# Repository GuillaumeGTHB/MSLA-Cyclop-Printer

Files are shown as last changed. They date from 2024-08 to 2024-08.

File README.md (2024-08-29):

# MSLA Cyclop Printer !
<p align="center">



</p>

If you like my work, you can help me by buying me a coffee, thank you! *https://buymeacoffee.com/guillaumehy or
 [paypal.me/guillaumehaouy](https://www.paypal.com/paypalme/guillaumehaouy)* <br />
*I should point out that I am a 20 year old student, it takes me a huge amount of time so don't be too harsh and impatient with me !* <br />
+ **A guide in .pdf format (English language, 64 pages for version 1.1) is included, it is a must-read, everything is explained in detail !** <br />
+ **NanoDLP is too huge for this repertory, you can download it at : https://www.nano3dtech.com/nanodlp-download/** <br />

**1. Introduction** <br />
**2. Technical details of the MSLA Cyclop printer** <br />
**3. Technical details of the Helios Curing station** <br />
**4. Pictures of my first prints (print tests take a lot of time, they are not yet 100% optimal)** <br />
**5. Schematics**
- A. Cyclop - 3D Printer
- B. Helios - Curing Station

## 1. Introduction
+ **Be careful! The resin severely attacks the printed plastic, as explained in the guide, you will need to apply a protective varnish on the tank as well as on the printing plate** <br />
+ Here you will find all the files and instructions on my homemade MSLA Cyclop v1.3 resin printer (and its Helios curing station) ! <br />
The CAD files (.step format) are available, the appropriate GRBl firmware as well as the NanoDLP version that I used. <br />
<p align="center">

 

 <br />
</p>

## 2. Technical details of the MSLA Cyclop printer <br />
+ Standalone printer (integrated slicer, just place an .stl file on a USB key) with Nextion 3.2" touch screen
+ Ultra-rigid structure in 2020 aluminum profiles
+ Ultra resolution axis ! Ball screw and two linear ball axes MGN12C
+ Electronics: Raspberry Pi 3B+ / Arduino Uno + Shield CNC v3 + A4988 driver (NanoDLP firmware for the RPI3B+, GRBL for the Arduino)<br />
+ Screen: 2k, 5.5" 1440p x 2560p <br />
+ Resolution: 47.25µm (0.04725mm) <br />
+ Printable area: 125x67x165mm <br />
+ UV power: 38W (adjustable in PWM with the M3 S1to1000 command) <br />
+ Approximate price: $450 <br />
+ Power supply: 12V 8A <br />
+ → more details in the .pdf guide <br />
<p align="center">




</p>

## 3. Technical details of the Helios Curing station <br />
+ Approximate power: 15W <br />
+ Turntable plate with adjustable timer <br />
+ Upward airflow (two 3010 fans: 30x10mm) <br />
+ Approximate price: $30 <br />
+ Minimum power supply: 12V 2A <br />
+ → more details in the .pdf guide <br />
<p align="center">




</p>

## 4. Pictures of my first prints
<p align="center">



</p>
<p align="center">


</p>

## 5. Schematics
### A. Cyclop
<p align="center">

</p>

### B. Helios
<p align="center">

</p>

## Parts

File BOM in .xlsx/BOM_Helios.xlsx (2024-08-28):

Name | Quantity | Links | Price | Total price
Timer module | 1 | https://fr.aliexpress.com/item/1005005994998871.html | 1.82 € | 1.82 €
LM2596 | 1 | https://fr.aliexpress.com/item/1082500515.html? | 0.94 € | 0.94 €
PWM 12V | 1 | https://fr.aliexpress.com/item/1005006462873434.html | 1.40 € | 1.40 €
16mm Led switch | 1 | https://fr.aliexpress.com/item/1005005617484886.html | 2.22 € | 2.22 €
3010 12V Fan | 2 | https://fr.aliexpress.com/item/1005003371996395.html | 0.99 € | 1.98 €
DC Jack Socket | 1 | https://fr.aliexpress.com/item/1005001368469076.html | 3.77 € | 3.77 €
Double side tape | /
Mirror tape | 5 | https://fr.aliexpress.com/item/1005003341029080.html | 3.17 € | 3.17 €
Turning Base | 1 | https://fr.aliexpress.com/item/1005006211006031.html | 7.88 € | 7.88 €
405nm Leds 12V | 2m | https://fr.aliexpress.com/item/4001062709706.html | 4.59 € | 4.59 €
5x3mm magnets | 8 | https://fr.aliexpress.com/item/1005001998183752.html | 1.24 € | 1.24 € | 29.01 €
M3x6 | 6
M3x8 | 8
M3x12 | 18
Spacer M3x5 | 4
M3 Inserts | 26

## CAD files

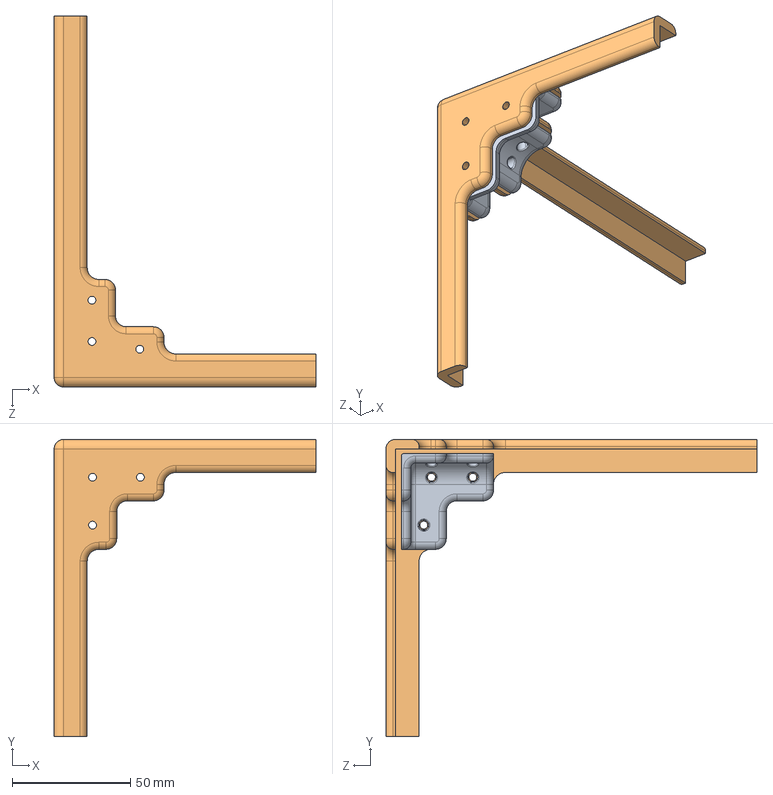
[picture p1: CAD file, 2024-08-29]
Cyclop - MSLA Printer - 3D files/Cyclop - STEP/Plexiglass_top_right.STEP
110.8 x 125.8 x 157.0 mm

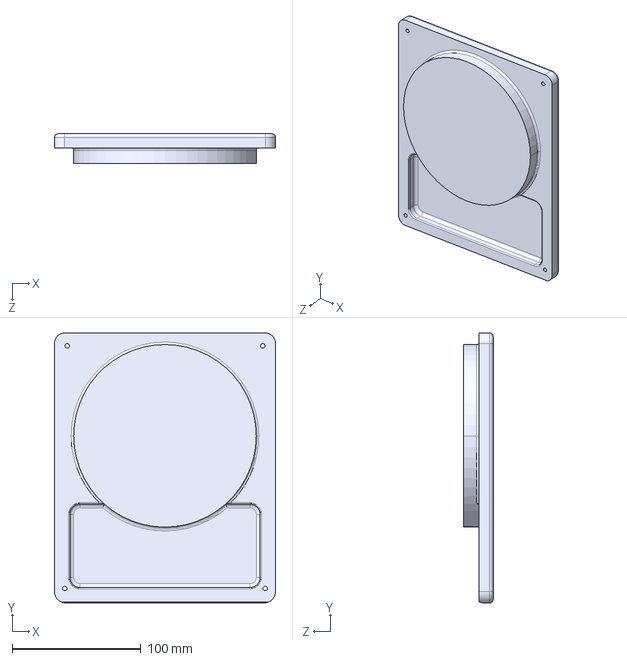
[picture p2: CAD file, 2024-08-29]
Helios - Curing Station - 3D files/Helios STEP/Base.STEP
172.0 x 210.0 x 23.0 mm

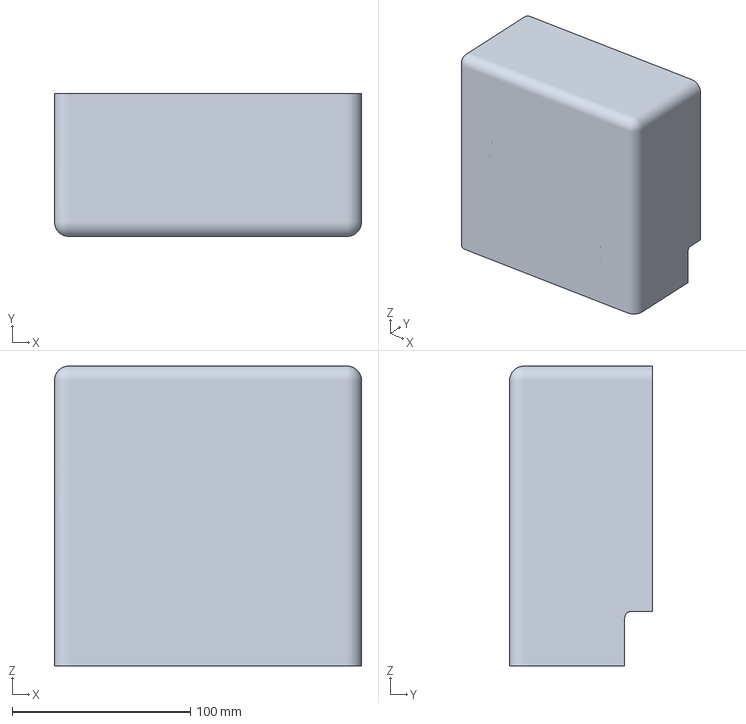
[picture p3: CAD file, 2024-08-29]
Helios - Curing Station - 3D files/Helios STL/Front_dual_colors.3MF
172.0 x 80.0 x 168.0 mm

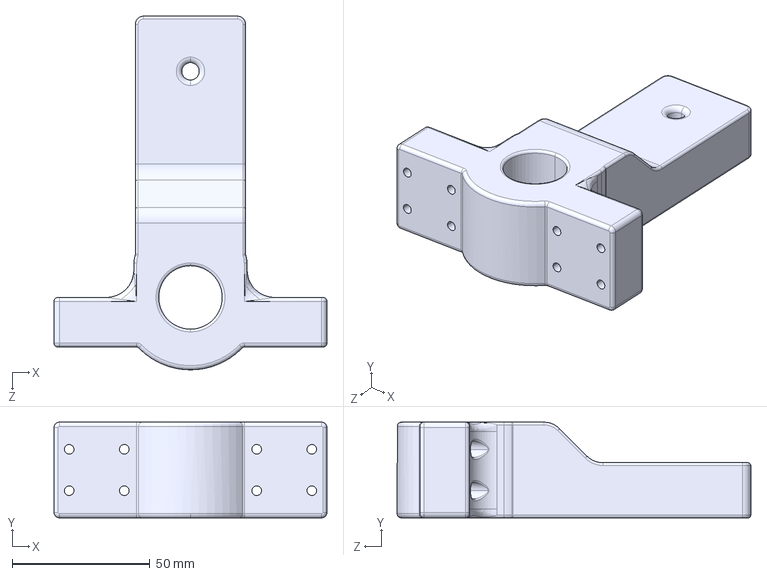
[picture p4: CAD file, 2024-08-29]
Cyclop - MSLA Printer - 3D files/Cyclop - STEP/Z_axis.STEP
99.0 x 34.7 x 128.2 mm

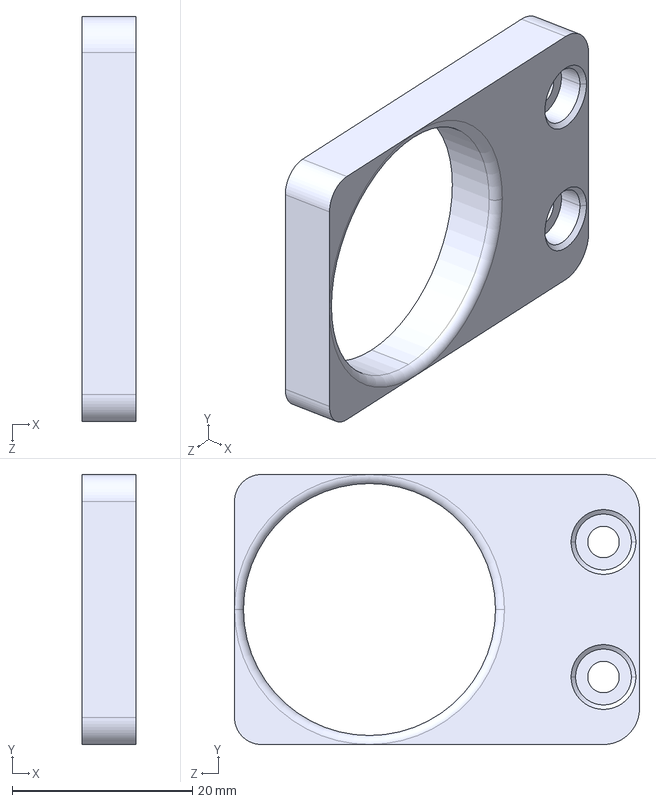
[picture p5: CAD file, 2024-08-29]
Helios - Curing Station - 3D files/Helios STEP/Ear.STEP
6.00 x 30.0 x 45.0 mm

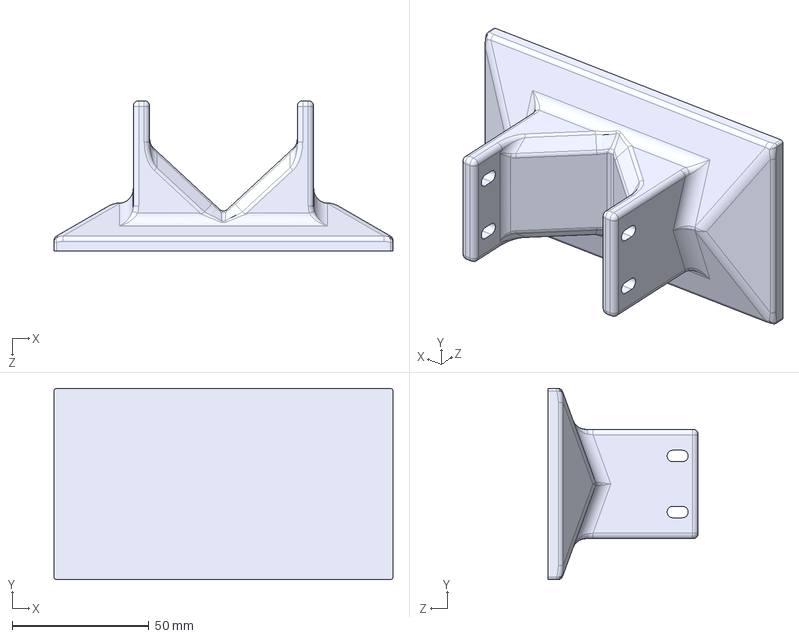
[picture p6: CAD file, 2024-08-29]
Cyclop - MSLA Printer - 3D files/Cyclop - STEP/Print_platform.STEP
124.0 x 70.0 x 55.0 mm

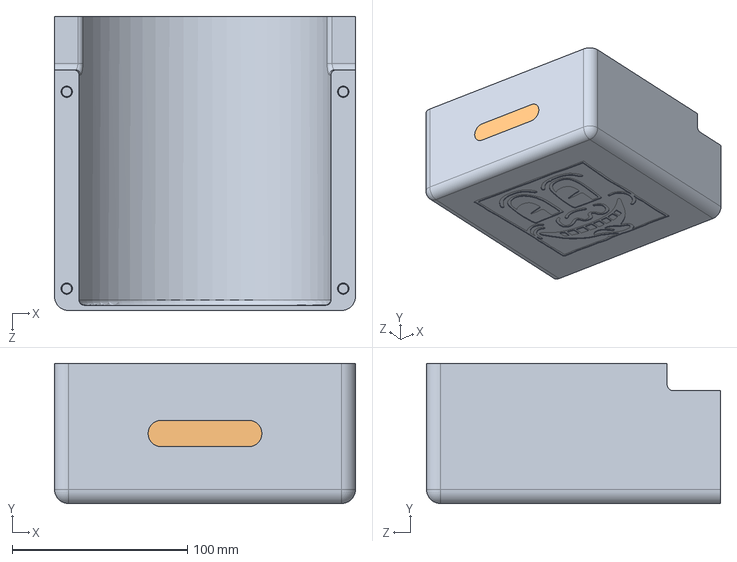
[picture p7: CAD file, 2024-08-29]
Helios - Curing Station - 3D files/Helios STEP/Front_mono_color.STEP
172.0 x 80.0 x 168.0 mm

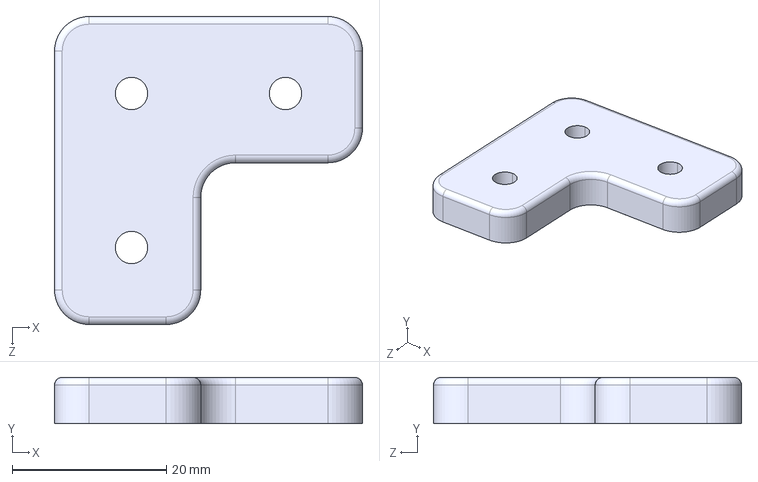
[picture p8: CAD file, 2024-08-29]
Cyclop - MSLA Printer - 3D files/Cyclop - STEP/Corner.STEP
40.0 x 6.00 x 40.0 mm

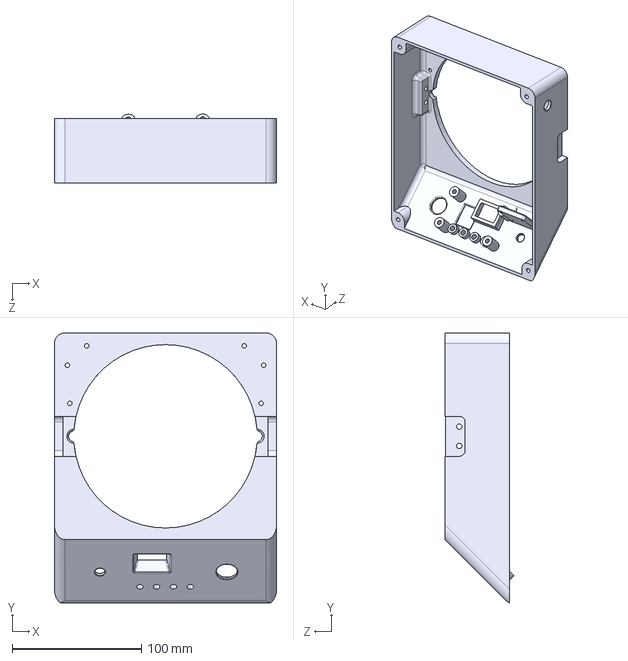
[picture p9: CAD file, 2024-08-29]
Helios - Curing Station - 3D files/Helios STEP/Box.STEP
172.0 x 209.1 x 53.4 mm

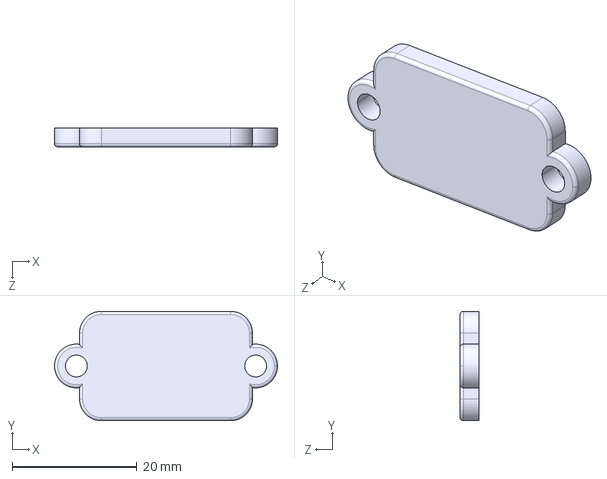
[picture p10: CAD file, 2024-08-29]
Cyclop - MSLA Printer - 3D files/Cyclop - STEP/Mipi_clamp.STEP
35.7 x 17.5 x 3.00 mm

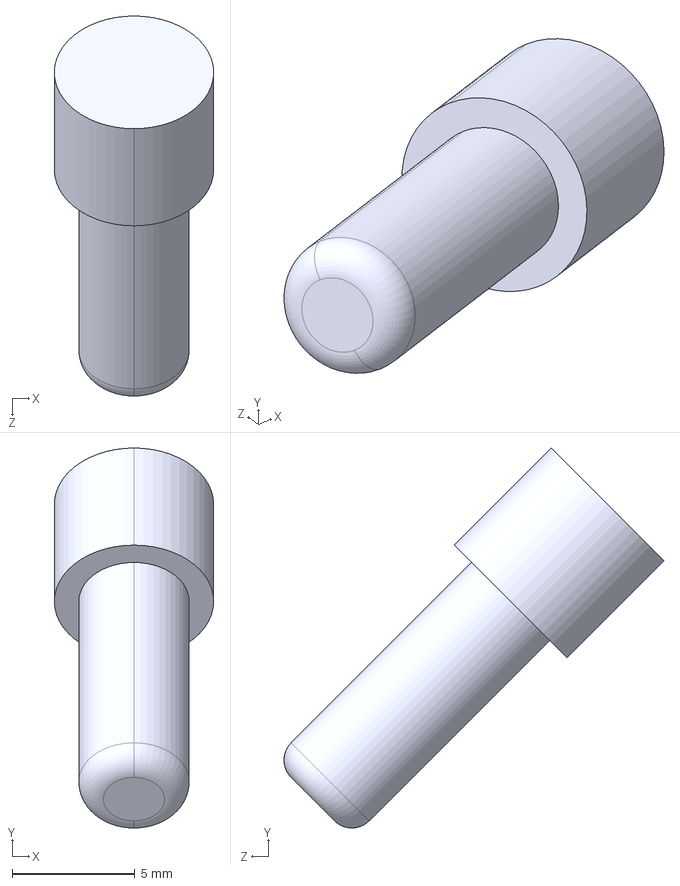
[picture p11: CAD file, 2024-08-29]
Helios - Curing Station - 3D files/Helios STEP/Spindle.STEP
6.50 x 15.5 x 15.5 mm

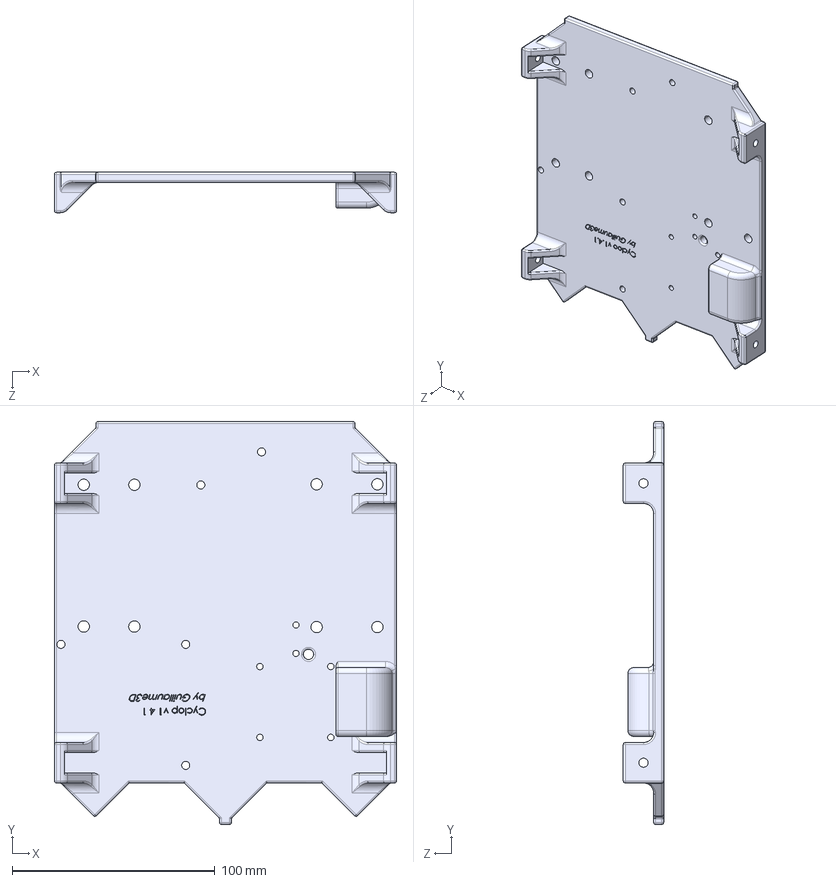
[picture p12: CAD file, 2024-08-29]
Cyclop - MSLA Printer - 3D files/Cyclop - STEP/Base.STEP
169.0 x 199.0 x 20.0 mm

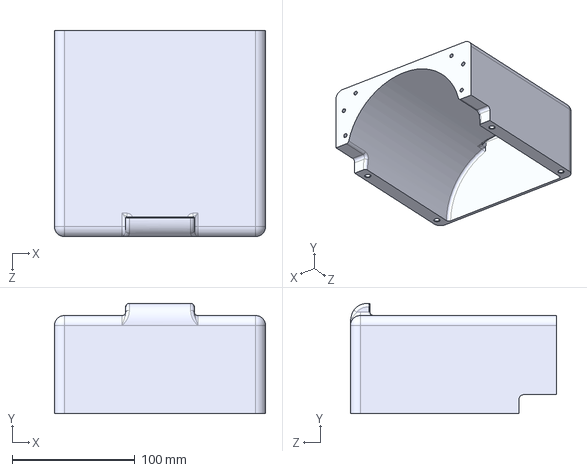
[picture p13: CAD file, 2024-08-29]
Helios - Curing Station - 3D files/Helios STEP/Back.STEP
172.0 x 90.0 x 168.0 mm

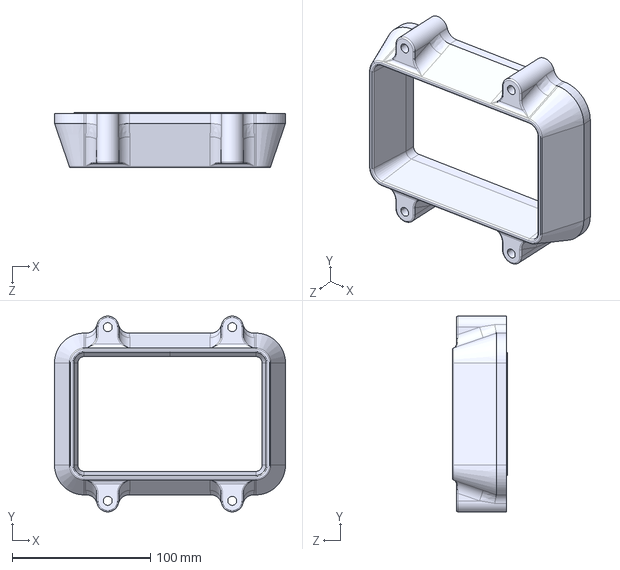
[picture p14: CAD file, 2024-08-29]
Cyclop - MSLA Printer - 3D files/Cyclop - STEP/Tank.STEP
167.0 x 141.5 x 40.0 mm

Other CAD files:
Cyclop - MSLA Printer - 3D files/Cyclop - STEP/Front_plate.STEP
Cyclop - MSLA Printer - 3D files/Cyclop - STEP/FEP_clamp.STEP
Cyclop - MSLA Printer - 3D files/Cyclop - STEP/Left_plate.STEP
Cyclop - MSLA Printer - 3D files/Cyclop - STEP/UV_cooling.STEP
Cyclop - MSLA Printer - 3D files/Cyclop - STEP/Back_plate.STEP
Cyclop - MSLA Printer - 3D files/Cyclop - STEP/Filter_box.STEP
Cyclop - MSLA Printer - 3D files/Cyclop - STEP/Filter_cap.STEP
Cyclop - MSLA Printer - 3D files/Cyclop - STEP/Foot.STEP
Cyclop - MSLA Printer - 3D files/Cyclop - STEP/Platform_clamp.STEP
Cyclop - MSLA Printer - 3D files/Cyclop - STEP/Plexiglass_base_left.STEP
Cyclop - MSLA Printer - 3D files/Cyclop - STEP/Plexiglass_base_right.STEP
Cyclop - MSLA Printer - 3D files/Cyclop - STEP/Plexiglass_top_left.STEP
Cyclop - MSLA Printer - 3D files/Cyclop - STEP/Reflector.STEP
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

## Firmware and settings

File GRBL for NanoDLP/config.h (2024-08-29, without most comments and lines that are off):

#define config_h
#include "grbl.h" // For Arduino IDE compatibility.
#define DEFAULTS_PEOPOLY_PHENOM
#define BAUD_RATE 115200
#define CPU_MAP_ATMEGA328P // Arduino Uno CPU
#define CMD_STATUS_REPORT '?'
#define CMD_FEED_HOLD '!'
#define CMD_CYCLE_START '~'
#define CMD_RESET '^' // stock is 0x18 - ctrl-x.
#define CMD_SAFETY_DOOR '@'
#define HOMING_CYCLE_0 (1<<Z_AXIS)                // REQUIRED: First move Z to clear workspace.
#define N_HOMING_LOCATE_CYCLE 1 // Integer (1-128)
#define N_STARTUP_LINE 2 // Integer (1-2)
#define N_DECIMAL_COORDVALUE_INCH 4 // Coordinate or position value in inches
#define N_DECIMAL_COORDVALUE_MM   3 // Coordinate or position value in mm
#define N_DECIMAL_RATEVALUE_INCH  1 // Rate or velocity value in in/min
#define N_DECIMAL_RATEVALUE_MM    0 // Rate or velocity value in mm/min
#define N_DECIMAL_SETTINGVALUE    3 // Decimals for floating point setting values
#define REPORT_REALTIME_RATE // Disabled by default. Uncomment to enable.
#define MESSAGE_PROBE_COORDINATES // Enabled by default. Comment to disable.
#define SAFETY_DOOR_SPINDLE_DELAY 4000
#define SAFETY_DOOR_COOLANT_DELAY 1000
#define ACCELERATION_TICKS_PER_SECOND 100
#define ADAPTIVE_MULTI_AXIS_STEP_SMOOTHING  // Default enabled. Comment to disable.
#define TOOL_LENGTH_OFFSET_AXIS Z_AXIS // Default z-axis. Valid values are X_AXIS, Y_AXIS, or Z_AXIS.
#define VARIABLE_SPINDLE // Default enabled. Comment to disable.
#define SPINDLE_MAX_RPM 1000.0 // Max spindle RPM. This value is equal to 100% duty cycle on the PWM.
#define SPINDLE_MIN_RPM 0.0    // Min spindle RPM. This value is equal to (1/256) duty cycle on the PWM.
#define REPORT_ECHO_LINE_RECEIVED // Default disabled. Uncomment to enable.
#define MINIMUM_JUNCTION_SPEED 0.0 // (mm/min)
#define MINIMUM_FEED_RATE 1.0 // (mm/min)
#define N_ARC_CORRECTION 12 // Integer (1-255)
#define ARC_ANGULAR_TRAVEL_EPSILON 5E-7 // Float (radians)
#define DWELL_TIME_STEP 50 // Integer (1-255) (milliseconds)
#if defined(USE_SPINDLE_DIR_AS_ENABLE_PIN) && !defined(VARIABLE_SPINDLE)
  #error "USE_SPINDLE_DIR_AS_ENABLE_PIN may only be used with VARIABLE_SPINDLE enabled"
#endif
#if defined(USE_SPINDLE_DIR_AS_ENABLE_PIN) && !defined(CPU_MAP_ATMEGA328P)
  #error "USE_SPINDLE_DIR_AS_ENABLE_PIN may only be used with a 328p processor"
#endif

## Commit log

2024-08-29 GRBL for Cyclop v1.3
    [config.h, cpu_map.h, defaults.h]
2024-08-29 Helios files, in .step and .stl
    [Back.STEP, Base.STEP, Base.stl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]
2024-08-29 Unzip to have the full assembly of Helios in .step
2024-08-29 .step & .stl files to building Cyclop Printer !
    [Back_plate.STEP, Back_plate.STL, Base.STEP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]

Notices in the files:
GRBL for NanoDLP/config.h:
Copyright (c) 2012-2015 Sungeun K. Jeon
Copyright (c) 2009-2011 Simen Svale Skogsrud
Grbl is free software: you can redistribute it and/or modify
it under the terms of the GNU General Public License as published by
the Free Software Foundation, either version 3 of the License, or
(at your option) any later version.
